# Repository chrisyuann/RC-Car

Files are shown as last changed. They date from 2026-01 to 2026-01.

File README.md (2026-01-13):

# Remote Controlled Self-Designed Car

## Intro
I want to create a remote controlled car intended for audiences of kids and teenagers. The goal is to make the car fun and easy to drive and control with a remote. I want my car to be unique, and I'm coming up with original ideas to create the main aspects of the car: the steering and differential. For the steering, I will create a belt-and-pulley system operated by a servo, rotating a four-bar linkage system. The car will be a rear wheel differential, preventing slippage when the car is making sharp turns.

Screenshot 2026-01-12 at 11 40 28 AM

^^Steering System^^

## Research
I researched about the differential. The basics include a pinion gear that rotates the sun gear, rotating the differential housing. The inner gears rotate along with the housing. When the car is turning, the differential allows the wheels to spin at different speeds with two different D-shafts.



The steering system also required research. The most common type of steering is the rack and pinion. This design is used on the majority of produced cars, which solidifies reliability. I looked at other steering systems as well. The crank and slider system also turns the wheels and is used in some vehicles. However, I decided to build my own, using a belt-and-pulley that rotates the wheels.



(Rack and Pinion)



(Crank and Slider)



(Belt and Pulley: My idea)

## Sketches, Modelling, Technical Specifications

### Steering System

Created rough sketching of the four-bar linkage system

Screenshot 2026-01-12 at 12 11 48 PM

Used existing hubs to mount the wheels to the shafts:

Screenshot 2026-01-12 at 12 12 19 PM

Wheel leg:

Screenshot 2026-01-12 at 12 12 39 PM

Assy:

Screenshot 2026-01-12 at 12 12 48 PM

I needed to figure out the ideal distance between the pulleys and I modeled it in CAD.

Screenshot 2026-01-12 at 12 02 50 PM

(At the point of intersection, the servo head and turning joint will be ideally placed)

I made my servo mount on that point.

Screenshot 2026-01-12 at 12 05 25 PM

Result:

Screenshot 2026-01-12 at 12 05 57 PM

Screenshot 2026-01-12 at 12 07 01 PM

### Differential

I used bevel gears found on McMaster Carr.

Screenshot 2026-01-12 at 12 08 12 PM

Created a rough outline of the inner gears.

Screenshot 2026-01-12 at 12 09 36 PM

## Electrical Components

My Main electrical components:

Servo:
Operates the steering system. I'm using the GoBilda 5-Turn Servo to have more than enough toleratnce for RC control -

Screenshot 2026-01-12 at 12 14 45 PM

Raspberry pi:
Brain of the Car; executes the code needed - 

Screenshot 2026-01-12 at 12 15 00 PM

DC Motor:
Operates the differential - 

Screenshot 2026-01-12 at 12 15 17 PM

H-Bridge Motor Driver:
Controls the DC Motor to operate the rear differential.

Screenshot 2026-01-12 at 3 06 47 PM

The red highlights are wired to power and black highlights are wired to ground and yellow highlights are wired to the GPIO pins.

In this simple H-bridge, we are creating a path from power to ground to move the motor forward. RPWM is to control the speed at which the motor moves. L_EN or Left Enable creates a path from power to ground to move the motor backward. LPWM is to control the speed at which the motor moves.

-

Screenshot 2026-01-12 at 12 15 37 PM

Buck Converter (12 V to 5 V)
Converts the 12 Volt batteries to 5 Volts to power microcontrollers such as raspberry pi, servo, etc. -

Screenshot 2026-01-12 at 12 15 56 PM

OAK-D Camera (Potential Addition) -

Screenshot 2026-01-12 at 12 16 20 PM

Rough electrical diagram:

Screenshot 2026-01-12 at 12 16 35 PM

## Software

The libraries I am using is GPIO and evdev. GPIO is a library to access the GPIO pins on the raspberry pi. I am going to control the servo and H-bridge motor driver by using these pins. Evdev is a library for device controllers such as the xbox controller. If I were using a wireless controller, I would bluetooth connect the controller to my raspberry pi, but I am using a wired one. I was able to read the device path here:

Screenshot 2026-01-12 at 7 06 37 PM

I was testing the raspberry pi: using GPIO 11 pin for PWM control for the steering, and using a buck converter to convert 12 volts into 5 volts to power the raspberry pi and servo. The controller is responding with values, but I am still in the process of troubleshooting, and I will ask others for help and may switch to have arduino as my microcontroller.

Screenshot 2026-01-12 at 7 08 22 PM

### Software Block Diagram

Screenshot 2026-01-12 at 7 10 34 PM

This logic fits with the evdev library. My initial code sets up the GPIO pins to be used. Then, I define variables for going forwards and backwards indicated for a specific GPIO pin. The H-bridge motor driver pinouts will be connected to the GPIO pins to open and close the H-circuit. I set up evdev library so I can read the xbox controller. I read for analog signals because I want to use the toggles that have variable power such as the joysticks and other analog buttons. I've set up the servo control to be the left joystick toggle and the forwards and backwards functions to be the top left and top right toggles. I'll update on future troubleshooting.

## Challenges and setbacks

I had many challenges. There were many dimension conflicts. For example, when I created one part of the system, there were things that I didn't consider. This included not positioning my back wheel bearing hole correctly to account for the front wheel position. This required a reiteration of my differential mount, DC Motor mount, and standoff heights. Another problem included not accounting for the diameter of the differential. I needed to reCAD the chassis, yet another reiteration.

When I was putting in the heat set inserts to the standoffs and other mounts, my lab didn't have the soldering iron that fits for M3 heat sets. Thus, I had to use the standard soldering iron, which created a larger margin for error in the angle tilt of the heat set. For a few standoffs, my heat set was angled slightly.

The chassis was also too big to be printed on the print bed of the 3D printer. I needed to split the chassis in half to print separately, and create heat sets to screw them together. The printing time was extremely long.

## Reflection as of 1/12/26
I finished my steering system and have developed my chassis. I am currently mounting my components and troubleshooting the differential. I am still working on making my car into something tangible, but as of now, the steering system is working successfully.

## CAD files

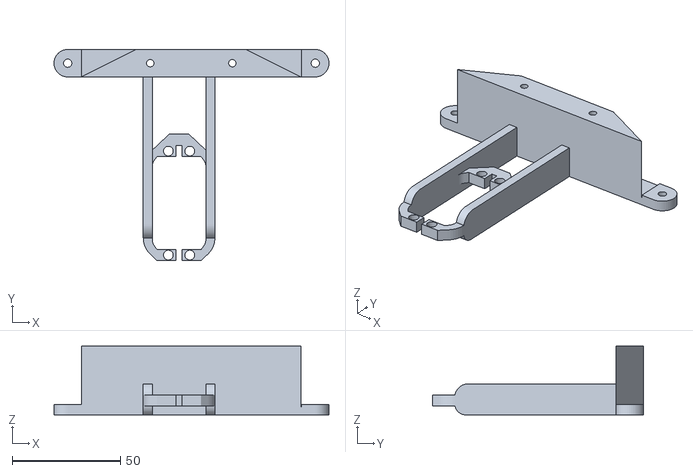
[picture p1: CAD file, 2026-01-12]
SERVO MOUNT.stl
127.0 x 97.5 x 31.8

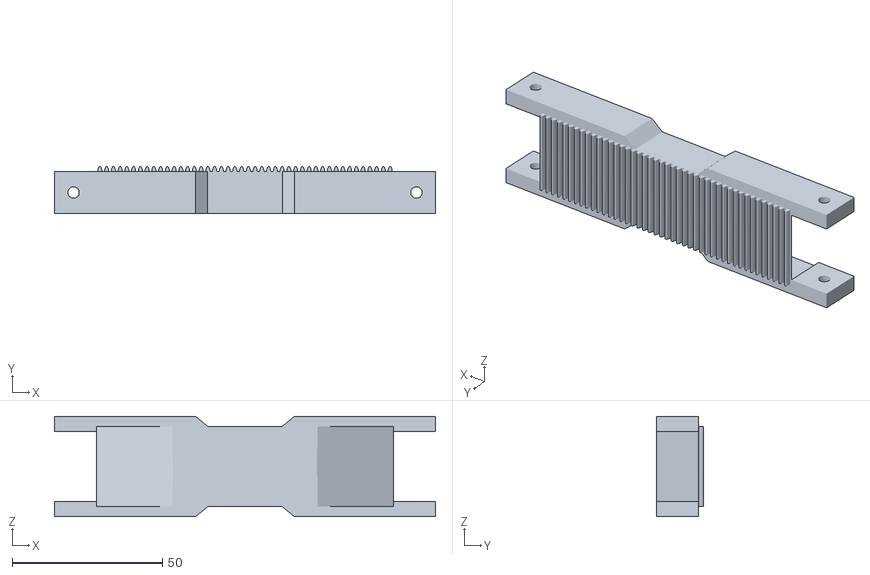
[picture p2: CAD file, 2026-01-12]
LINKAGE BAR.stl
127.0 x 15.5 x 33.5

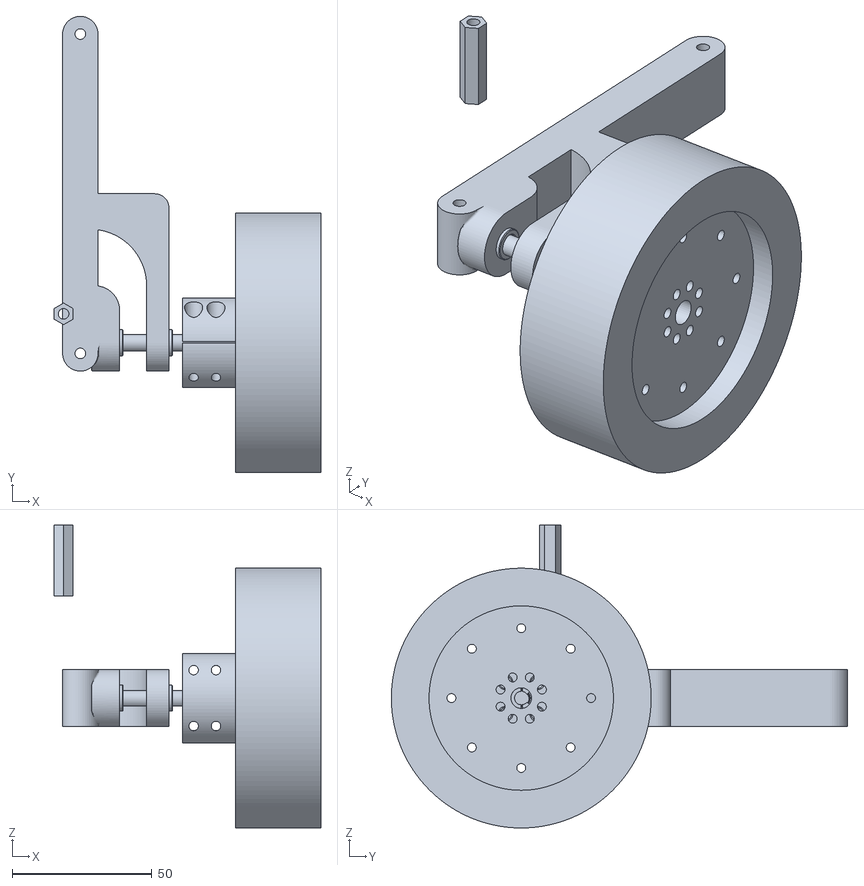
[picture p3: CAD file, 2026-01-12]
WHEEL LEG.stl
95.4 x 163.3 x 108.5

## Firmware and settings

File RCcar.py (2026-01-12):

import evdev
import numpy as np
import RPi.GPIO as GPIO
import time

# --- GPIO setup ---
GPIO.setmode(GPIO.BOARD)

# Servo setup (steering)
GPIO.setup(11, GPIO.OUT)
servo = GPIO.PWM(11, 50)  # 50 Hz
servo.start(0)

# DC motor setup (differential)
GPIO.setup(29, GPIO.OUT)
GPIO.setup(31, GPIO.OUT)
pinOneMotor_PWM = GPIO.PWM(29, 10000)  # 10 kHz
pinTwoMotor_PWM = GPIO.PWM(31, 10000)
pinOneMotor_PWM.start(0)
pinTwoMotor_PWM.start(0)

# --- Helper function ---
def map_value(value, in_min, in_max, out_min, out_max):
    return np.interp(value, [in_min, in_max], [out_min, out_max])

# Motor control functions
def forward(speed):
    GPIO.output(31, False)
    pinOneMotor_PWM.ChangeDutyCycle(speed)

def backward(speed):
    GPIO.output(29, False)
    pinTwoMotor_PWM.ChangeDutyCycle(speed)

# --- Controller setup ---
device = evdev.InputDevice("/dev/input/event2")  # replace with your actual device

try:
    for event in device.read_loop():
        if event.type == evdev.ecodes.EV_ABS:
            # Steering (left stick X-axis)
            if event.code == evdev.ecodes.ABS_X:
                angle = round(map_value(event.value, 0, 65535, 2, 12))
                servo.ChangeDutyCycle(angle)
                print(f"Steering angle: {angle}")

            # Right Trigger - Forward
            elif event.code == evdev.ecodes.ABS_GAS:
                speed = round(map_value(event.value, 0, 1023, 0, 100))
                forward(speed)
                print(f"Forward speed: {speed}%")

            # Left Trigger - Backward
            elif event.code == evdev.ecodes.ABS_BRAKE:
                speed = round(map_value(event.value, 0, 1023, 0, 100))
                backward(speed)
                print(f"Backward speed: {speed}%")

except KeyboardInterrupt:
    pass
finally:
    # Stop PWM and cleanup GPIO
    servo.stop()
    pinOneMotor_PWM.stop()
    pinTwoMotor_PWM.stop()
    GPIO.cleanup()

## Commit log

2026-01-12 Adding device path
2026-01-12 Create CAD parts
